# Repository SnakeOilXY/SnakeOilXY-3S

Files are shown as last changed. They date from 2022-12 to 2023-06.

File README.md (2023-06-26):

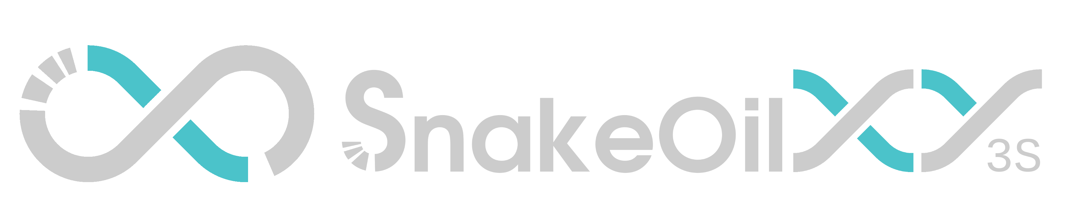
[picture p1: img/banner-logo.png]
Banner-logo


<a href="https://discord.gg/WZVP2HuAag" style="height: 40px !important;">Join us on Discord</a>

<a href='https://www.amazon.jp/hz/wishlist/ls/2AHXTCG01RYAZ?ref_=wl_share' target='_blank'>Buy Me a spool at amazon Japan</a>
<a href='https://www.printables.com/model/348118-snakeoilxy-3s/files' target='_blank'>download link</a>

# SnakeOilXY-3S
Entry level, low cost mod for Kingroon KP3S 3D printer.

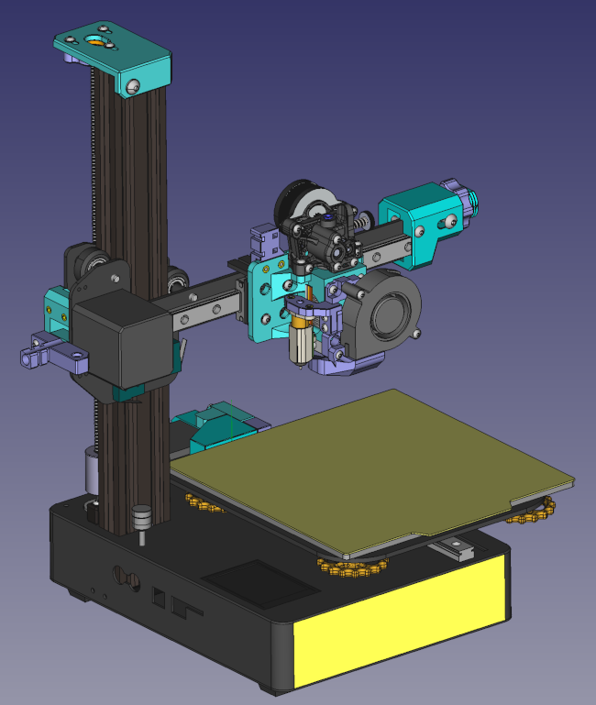
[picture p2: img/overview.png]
overview


## 1. Introduction

Kingroon KP3S is a nice small printer, but it comes with some mechanical design problems. This mod is aiming at fixing there problem with the lowest cost as possible.

__*This mod is for people already bought the KP3/S. DO NOT buy the KP3/S just because of this mod. There are many better printers you can build with the same price. For example [The Tic-Tac](https://www.printables.com/model/164038-tic-tac-miniaturised-v-minion)__

__*This mod is designed by measuring the real hardware of the first revision of the KP3(the model with Creality style direct red extruder). Some parts might need some minnor modify to fit other revisons of the machine.__

## 2. The problems and solutions

### 2.1. X and Y axis

- There is no proper way to adjust the belt tension of X and Y axis
- The belt path is not straight. This will affect the printed part dimension based on where it printed on the build place, special on large model.

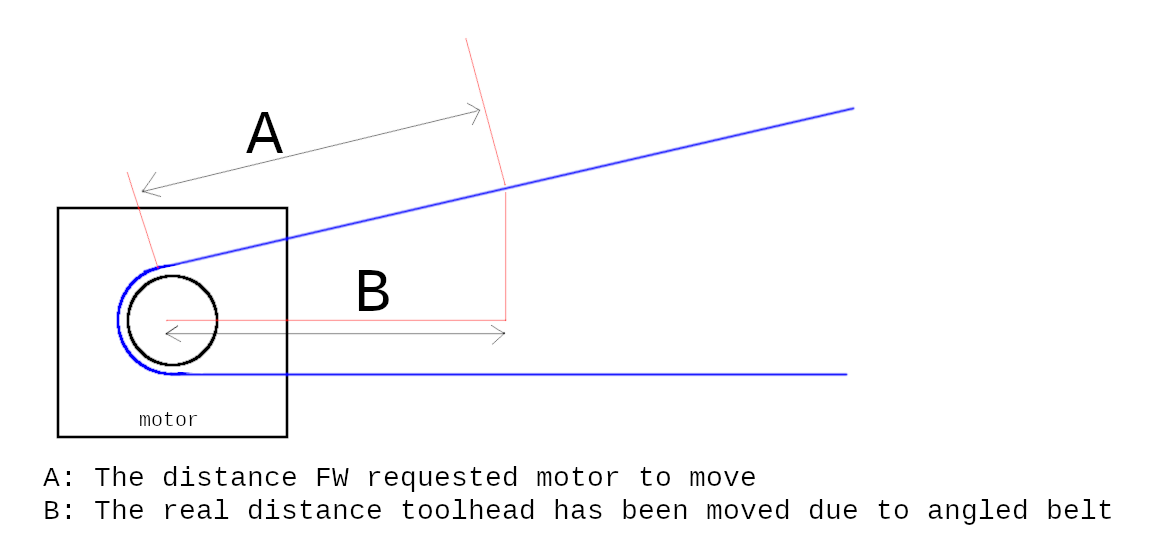
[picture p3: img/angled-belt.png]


- This mod added belt tensioner for X and Y axis.
- Change the belt mounting method to make the belt path straight.(check image bellow, this method apply for both X and Y belt).
- All motor shafts are supported by bearing.
- You will need new belts for XY tensioner mod since the belt path is a little longer than the original design. If not using my toolhead, you might need to your toolhead mounter to get full X movement.

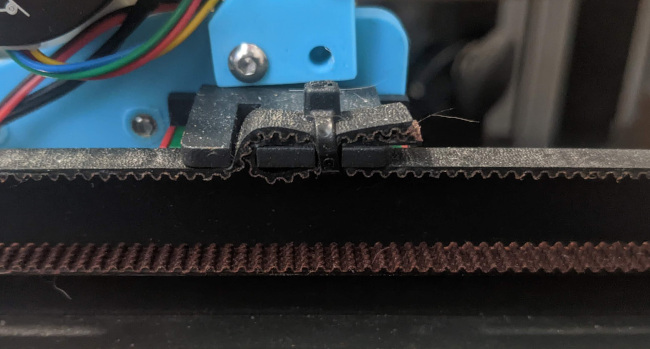
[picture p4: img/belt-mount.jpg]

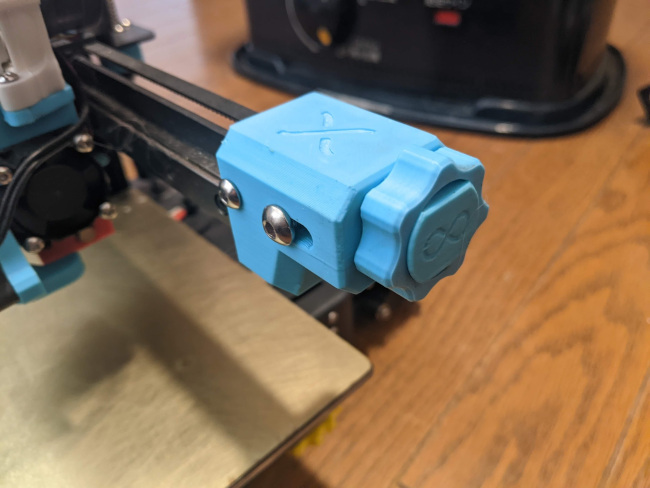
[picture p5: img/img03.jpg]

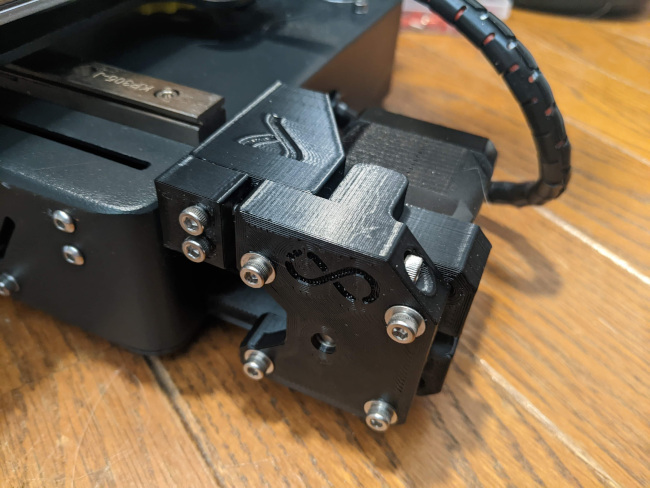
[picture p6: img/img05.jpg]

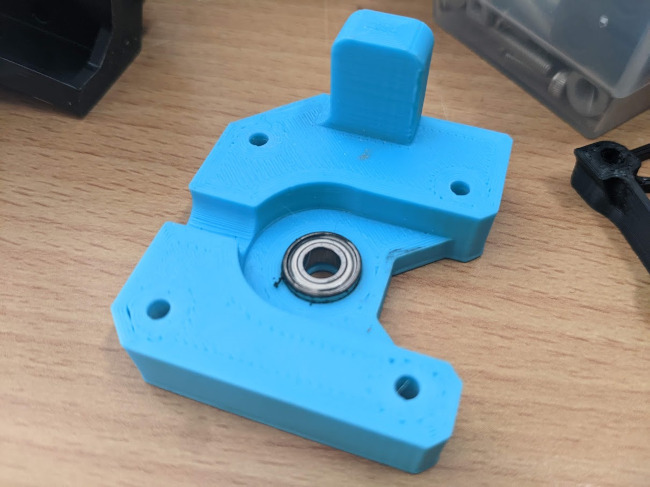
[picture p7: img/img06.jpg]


### 2.2. Z axis

- On some revisions of KP3/S the Z motor center and leadscrew nut are not well aligned. This will make the leadscew wobble and result in Z banding problem. 
- This mod added Oldham coupler and Position adjustable top support bearing. 
- Position adjustable top support bearing will allow to fine-adjust the leadscrew position so it parallel to the Z v-slot extrusion.
- Oldham coulper will deal with axial and angular misalignments of the leadscew nut.

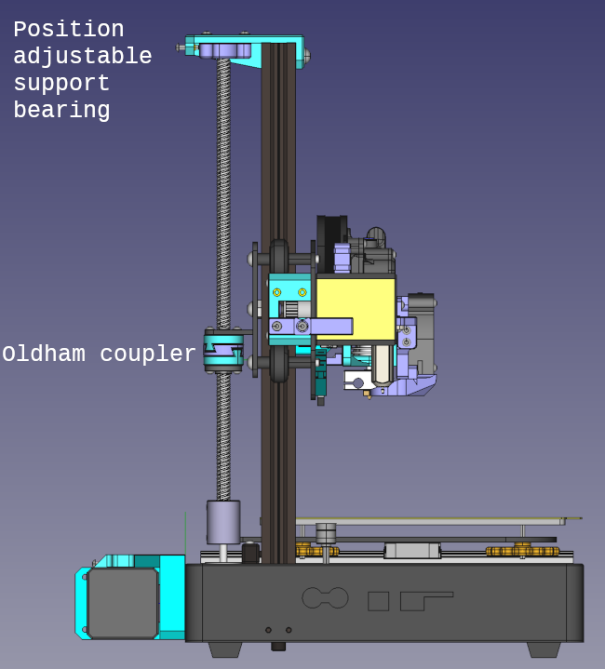
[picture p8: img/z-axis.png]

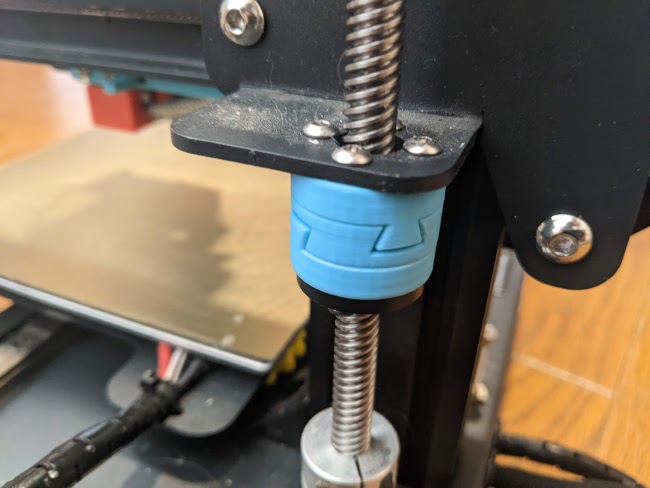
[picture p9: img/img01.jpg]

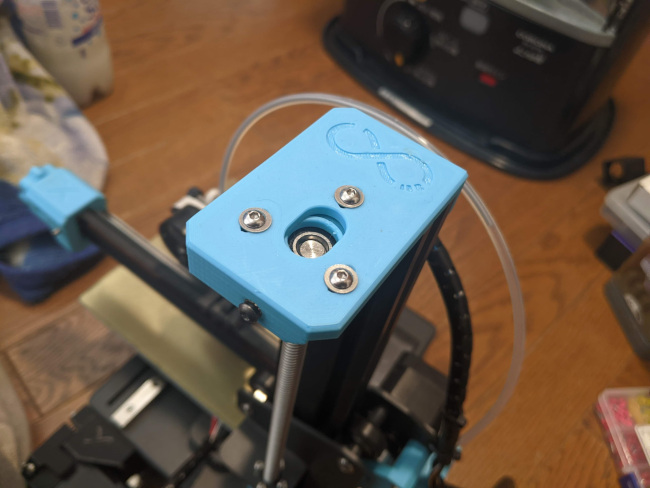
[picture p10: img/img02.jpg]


### 2.3. E axis (optional)

- There is no problem with the original extruder except it too heavy for the unsupported gantry. 
- This mod added 2 options for lighter extruder: Direct drive Sherpa mini mount and bowden extruder mount. 
- The above extruder mounters can be use with V6 hotend or any other hotend using the same mounting method(Dragon hotend with groove adapter for example).
- Optional mounting slot for BLtouch/3Dtouch
- Compatible with [bear_extruder_and_x_axis](https://github.com/gregsaun/bear_extruder_and_x_axis) fan duct and other 3rd party ducts like [RH_Dreambox's Air nozzle for the Bear extruder (Rev.1)](https://www.thingiverse.com/thing:3390107) or [MajorOCD's Fan Duct for Bear Extruder](https://www.thingiverse.com/thing:3855570)

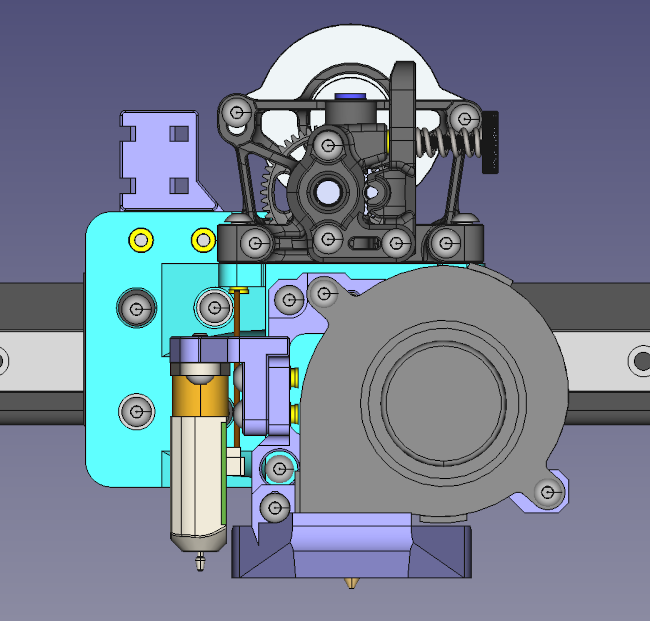
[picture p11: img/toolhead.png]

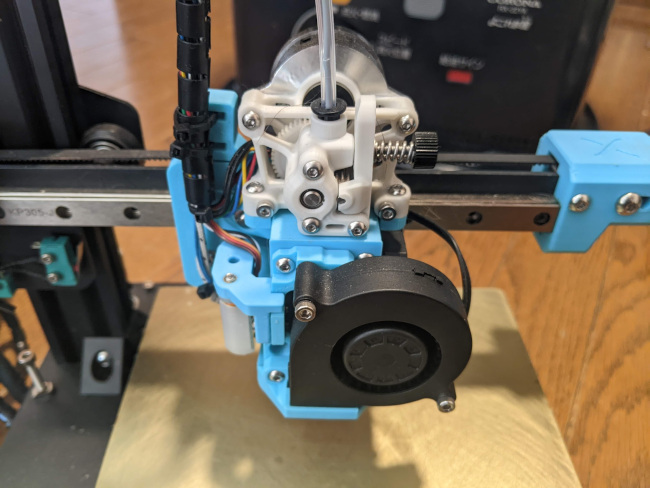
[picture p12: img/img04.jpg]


### 2.4. Klipper config

- will be added soon

## 3. Bill of materials

<table>
    <thead>
        <tr>
            <th>Item</th>
            <th>Quantity</th>
            <th>Description</th>
            <th>link</th>
        </tr>
    </thead>
    <tbody>
        <tr>
            <td>M3x4-HeatSet</td>
            <td>100</td>
            <td>M3 X D4.2 X L4.0</td>
            <td><a href="https://s.click.aliexpress.com/e/_Ad1n92" rel="nofollow">Aliexpress</a></td>
        </tr>
        <tr>
            <td>MR115 bearing</td>
            <td>2</td>
            <td></td>
            <td><a href="https://s.click.aliexpress.com/e/_De3O1rt" rel="nofollow">Aliexpress</a></td>
        </tr>
        <tr>
            <td>688 bearing</td>
            <td>1</td>
            <td></td>
            <td><a href="https://s.click.aliexpress.com/e/_Dd0g23b" rel="nofollow">Aliexpress</a></td>
        </tr>
        <tr>
            <td>20T 6mm Tooth Idler (5mm bore)</td>
            <td>2</td>
            <td>Only E3D's Gates idler or Mellow's Gates idler will fit</td>
            <td><a href="https://www.aliexpress.com/item/33023133633.html" rel="nofollow">Aliexpress</a></td>
        </tr>
        <tr>
            <td>6mm 2GT belt</td>
            <td>1.5~2m</td>
            <td>M3 X D4.2 X L4.0</td>
            <td><a href="https://www.Aliexpress.com/item/32952396111.html" rel="nofollow">Aliexpress</a></td>
        </tr>
        <tr>
            <td>4x5x12mm brass tube (IDxODxLength)</td>
            <td>1</td>
            <td>Can be cuted from longer tube</td>
            <td><a href="https://s.click.aliexpress.com/e/_DC6Dbc3" rel="nofollow">Aliexpress</a></td>
        </tr>
        <tr>
            <td>2.5mm wide ziptie</td>
            <td>1 pack</td>
            <td></td>
            <td></td>
        </tr>
        <tr>
            <td>Sherpa mini extruder kit</td>
            <td>1</td>
            <td>Direct extruder parts - OPTIONAL</td>
            <td><a href="https://s.click.aliexpress.com/e/_DmmcVKn" rel="nofollow">Aliexpress</a></td>
        </tr>
        <tr>
            <td>5015 blower fan</td>
            <td>1</td>
            <td>Direct extruder parts - OPTIONAL</td>
            <td><a href="https://s.click.aliexpress.com/e/_DllkWdp" rel="nofollow">Aliexpress</a></td>
        </tr>
        <tr>
            <td>3010 fan</td>
            <td>1</td>
            <td>Direct extruder parts - OPTIONAL</td>
            <td><a href="https://s.click.aliexpress.com/e/_DlSF5np" rel="nofollow">Aliexpress</a></td>
        </tr>
        <tr>
            <td>PTFE tube clip set</td>
            <td>2</td>
            <td>Extruder parts - OPTIONAL</td>
            <td><a href="https://s.click.aliexpress.com/e/_DEVMtuF" rel="nofollow">Aliexpress</a></td>
        </tr>
        <tr>
            <td>Bolts and nuts</td>
            <td>?</td>
            <td>Work-in-Progress</td>
            <td></td>
        </tr>
    </tbody>
</table>

## 4. How to print parts

- PETG, ABS or PC filament depend on your budget and how hot you will run the printer.
- 0,4mm nozzle, 0.2mm layer height, 5 walls, 30% infill
- Oldham coupler will need to be printed with small layer height(0.05~0.1mm) and small diameter nozzle(~0.25mm) if possible. This parts will need some sanding to make the mating surface smooth enough.

## 5. Copyright Notice

- [Sherpa mini extruder](https://github.com/Annex-Engineering/Sherpa_Mini-Extruder) is an original work of [Annex Engineering](https://github.com/Annex-Engineering), modified parts using their source code/design files are re-released under [ANNEX Engineering License](https://github.com/Annex-Engineering/ANNEX-Engineering-License-Agreement/blob/main/LICENSE.md).
- [bear_extruder_and_x_axis](https://github.com/gregsaun/bear_extruder_and_x_axis) is an original work of [Grégoire Saunier](https://github.com/gregsaun), modified parts using their source code/design files are re-released under [GNU General Public License v3.0](https://github.com/gregsaun/bear_extruder_and_x_axis/blob/master/LICENSE)
- The CAD assembly using Kingroon KP3/S model of [Fukuma Yohei](https://www.thingiverse.com/fukumay/designs) at [Thingiverse - Kingroon KP3S full assembly STP/OBJ data](https://www.thingiverse.com/thing:4889303) under [Creative Commons - Attribution license](https://creativecommons.org/licenses/by/4.0/)
- This printer design(SnakeOilXY-3S), it's document and software are released under [GNU General Public License v3.0](https://github.com/ChipCE/SnakeOil-XY/blob/master/LICENSE)

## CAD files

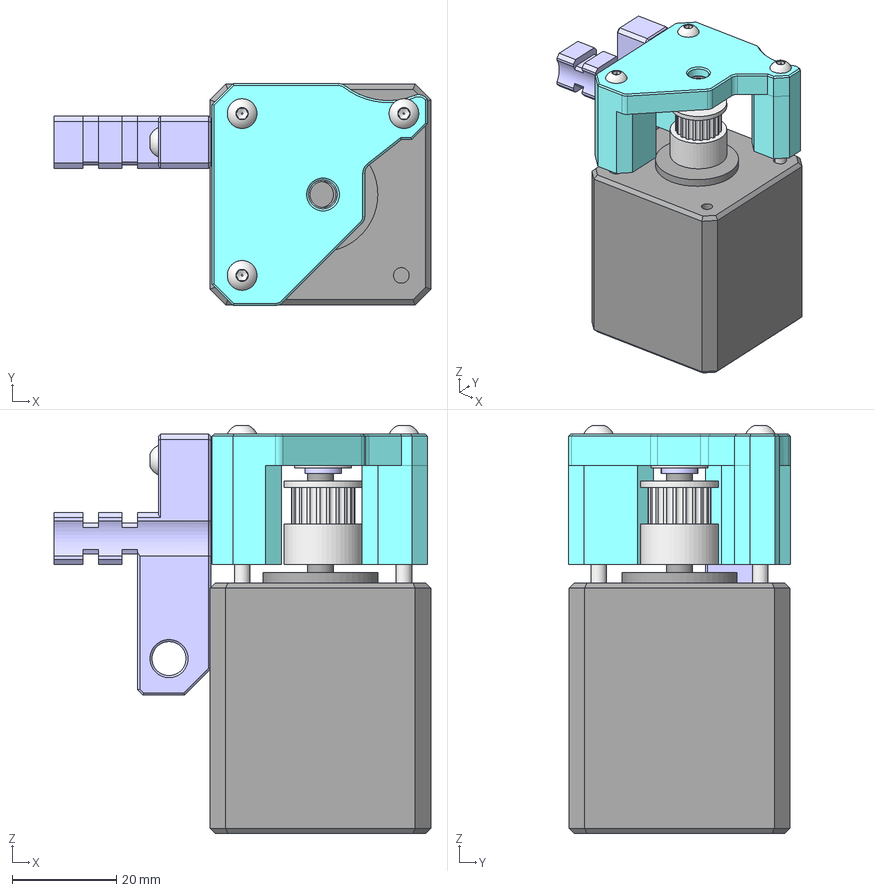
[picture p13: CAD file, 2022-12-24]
src/component-assembly/x-motor-support-assembly.FCStd
72.2 x 42.5 x 78.2 mm
x-motor-support
direct-drive-extruder-cable-mount
M3x30-Screw
M3x30-Screw003
M3x30-Screw004
M3x30-Screw005
M3-Insert
M3-Insert004
M3-Insert005
M3-Insert006
M3x12-Screw
MR115ZZ-bearing
stepper-motor
6mm-pulley
spacer-1mm

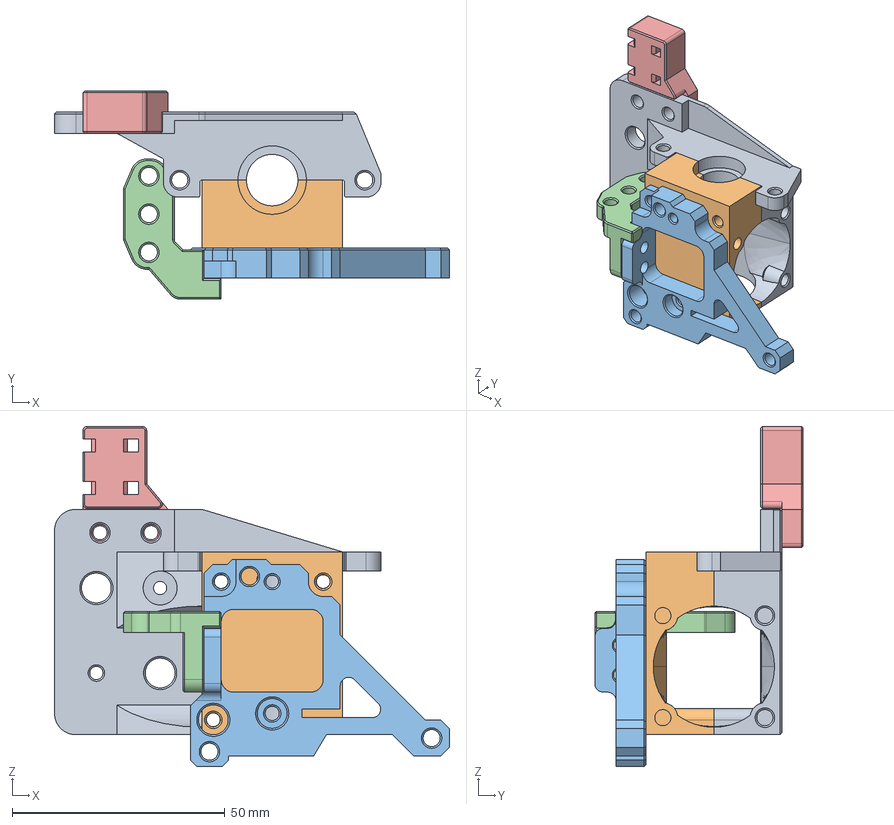
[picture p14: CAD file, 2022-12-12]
WIP/component-assembly/toolhead-assembly.FCStd
92.9 x 49.0 x 80.0 mm
back-body-direct
front-body
fan-mounter001
cable-mounter001

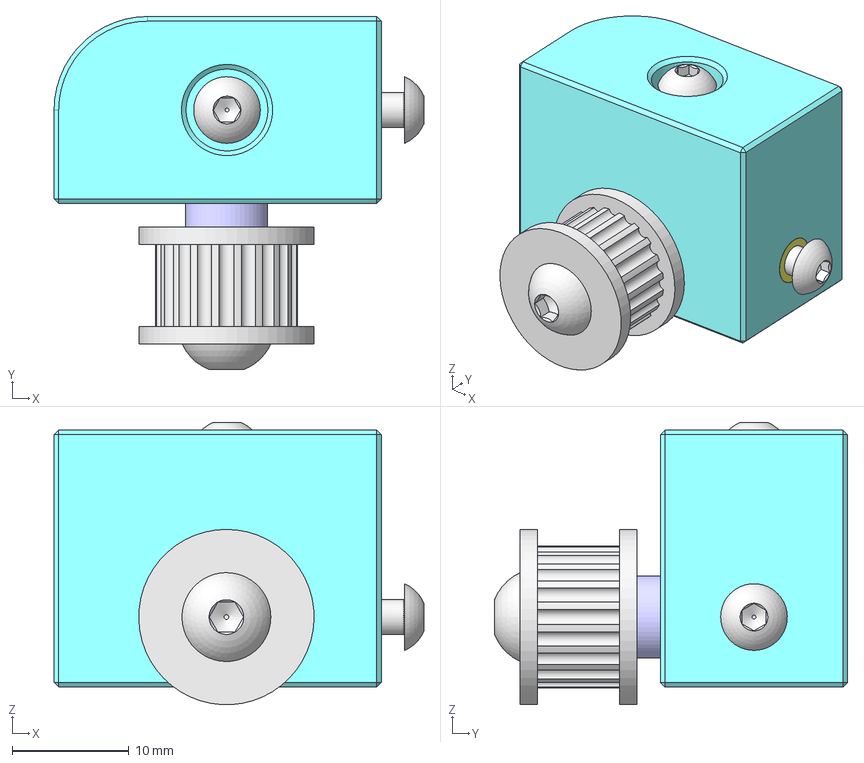
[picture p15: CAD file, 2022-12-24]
src/component-assembly/y-idler-supporter-assembly.FCStd
31.7 x 30.2 x 24.1 mm
shaft-supporter
spacer-2mm
6mm-tooth-idler001
brass-tube-4x5x12
M4x20-Screw
M3-HeatSet
M3-HeatSet001
M3x10-Screw
M3x12-Screw

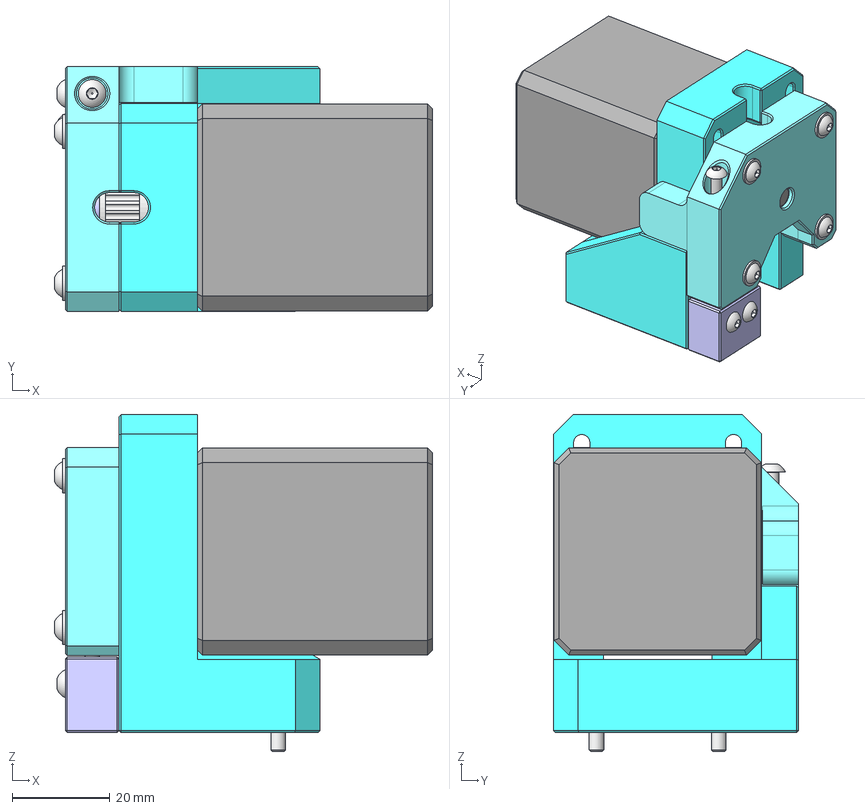
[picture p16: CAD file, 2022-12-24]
src/component-assembly/y-motor-mount-assembly.FCStd
77.2 x 50.0 x 68.8 mm
y-motor-mounter
y-motor-cap
tesioner-block
MR115ZZ-bearing
stepper-motor
M3-Insert
M3-Insert001
M3-Insert002
M3-Washer
M3-Washer001
M3-Washer002
M3-Washer003
M3x30-Screw
M3x30-Screw004
M3x30-Screw005
M3x30-Screw006
M3x30-Screw009
M3x30-Screw010
M3x40-Screw
M3-Washer006
M3-Washer007
M3x16-Screw
M3x16-Screw001
6mm-pulley
spacer-1mm

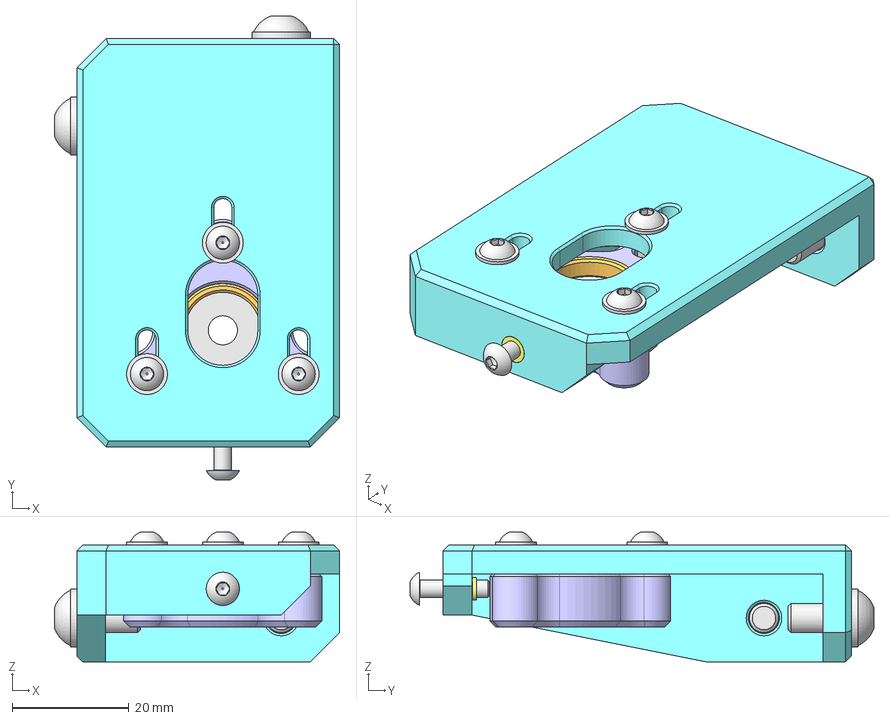
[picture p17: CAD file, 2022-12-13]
src/component-assembly/z-top-bearing-assembly.FCStd
48.9 x 79.5 x 22.2 mm
spacer
bearing-housing
M3-Insert
M3-Insert001
M3-Insert002
M3-Insert003
M3x12-Screw
M3-Washer
M3-Washer005
M3-Washer006
M3x14-Screw
M3x14-Screw003
M3x14-Screw004
M5-Washer
M5-Washer001
M5x12-Screw
M5x12-Screw001
top-plate
625-bearing

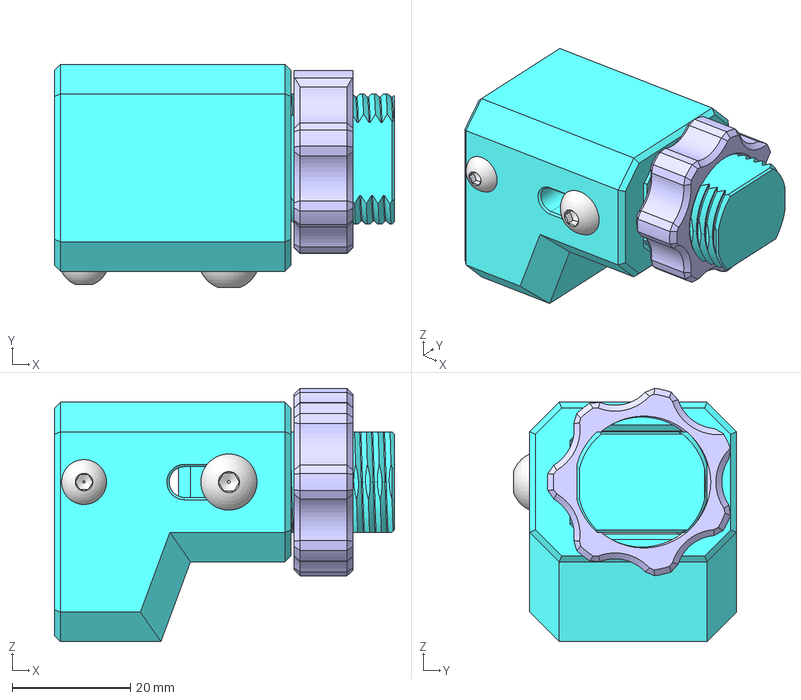
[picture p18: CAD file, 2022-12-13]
src/component-assembly/x-tesioner-assembly.FCStd
57.5 x 37.8 x 42.9 mm
pulley-housing
tensioner-body
tesioner-nut
M4x35-Screw
M5x35-Screw
6mm-tooth-idler001

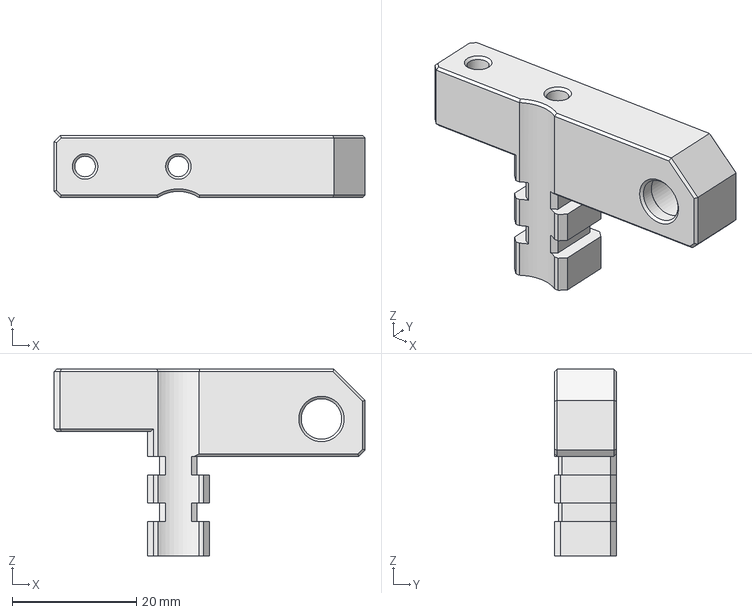
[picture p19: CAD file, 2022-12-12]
src/E-axis/direct-extruder-cable-mounter.FCStd
50.0 x 10.0 x 30.0 mm

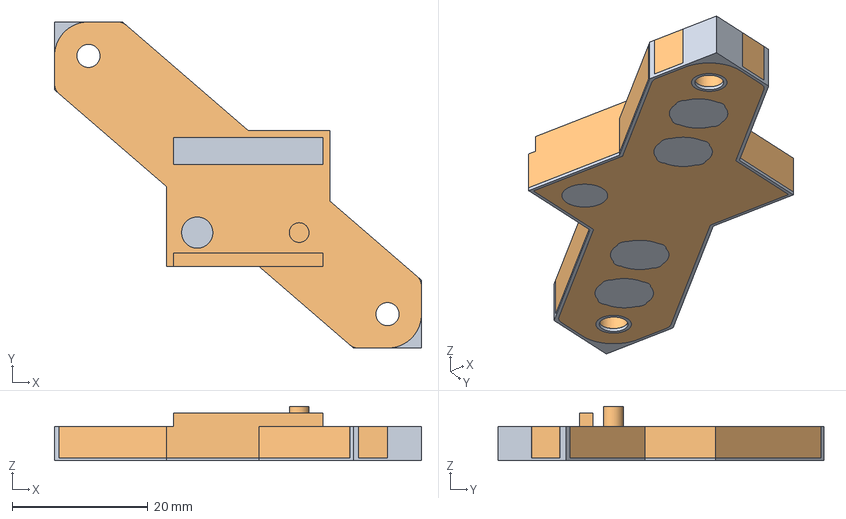
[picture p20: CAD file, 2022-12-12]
src/Other/adxl345-mounter.FCStd
54.0 x 48.0 x 8.00 mm

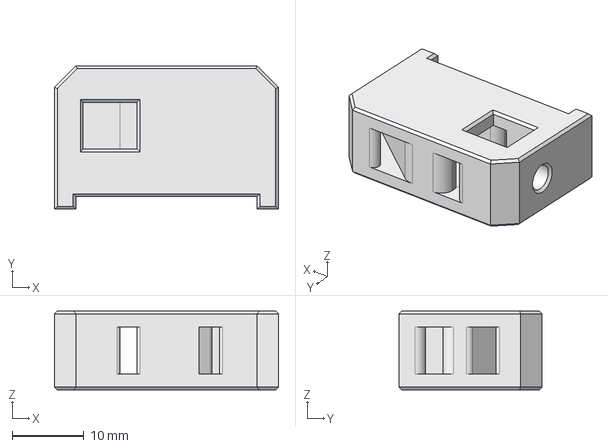
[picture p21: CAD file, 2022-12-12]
src/X-axis/belt-clip-tesioner.FCStd
31.3 x 20.0 x 11.0 mm

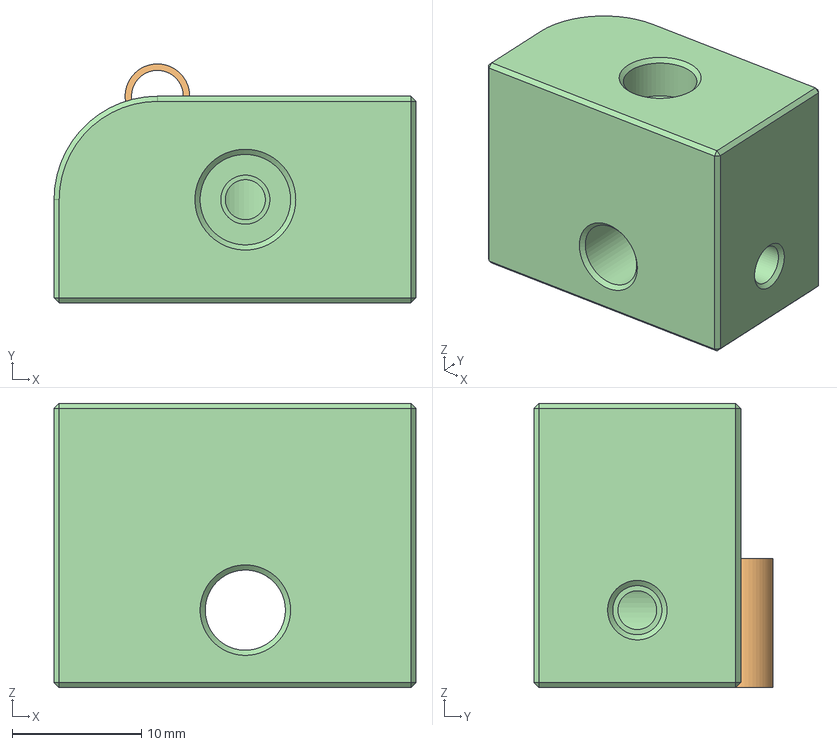
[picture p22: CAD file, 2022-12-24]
src/Y-axis/idler-supporter.FCStd
28.0 x 18.5 x 22.0 mm
brass-tube
brass-tube001

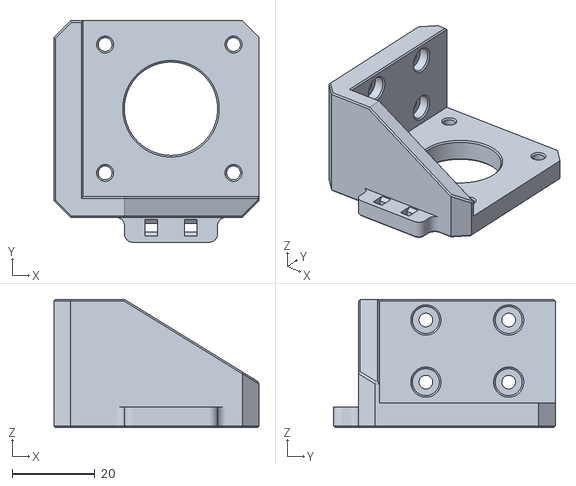
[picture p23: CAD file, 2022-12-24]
STLs/E-axis/OPTIONAL_1x_bowden-e-motor-mount.stl
49.5 x 53.5 x 31.0

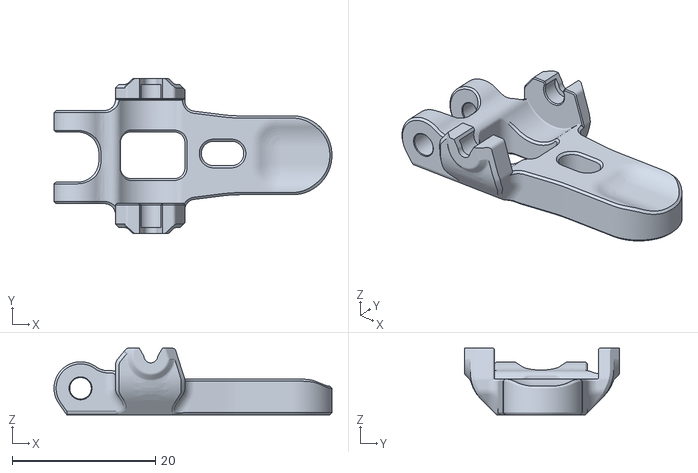
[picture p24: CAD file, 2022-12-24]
STLs/E-axis/sherpa-mini-extruder/filament-arm.stl
38.8 x 21.6 x 9.30

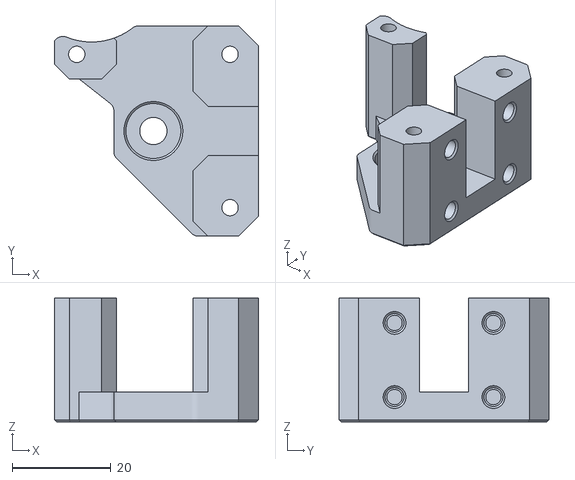
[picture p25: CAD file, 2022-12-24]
STLs/X-axis/x1_x-motor-support.stl
41.2 x 42.5 x 25.0

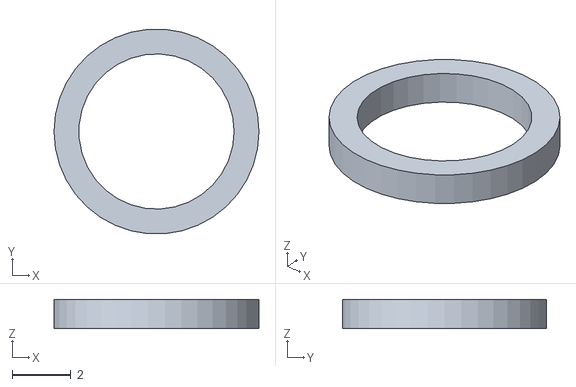
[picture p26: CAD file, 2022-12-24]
STLs/Y-axis/x1_motor-shaft-spacer.stl
7.00 x 6.98 x 1.00

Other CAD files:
STLs/Z-axis/x1_z-bearing-housing.stl
src/E-axis/back-body-bowden.FCStd
src/Other/belt-extra-mounter.FCStd
src/X-axis/x-belt-tensioner.FCStd
STLs/E-axis/1x_back-body-for-direct-drive.stl
STLs/E-axis/1x_bear-duct.stl
STLs/E-axis/1x_bltouch-mount.stl
STLs/E-axis/1x_cable-mounter.stl
STLs/E-axis/1x_front-body.stl
STLs/E-axis/1x_mounting-plate.stl
STLs/E-axis/1x_x-endstop.stl
STLs/E-axis/OPTIONAL_1x_back-body-for-bowden.stl
STLs/E-axis/sherpa-mini-extruder/back-body.stl
STLs/E-axis/sherpa-mini-extruder/front-body.stl
STLs/E-axis/x1_direct-drive-extruder-cable-mount.stl
STLs/X-axis/1x_idler-housing.stl
STLs/X-axis/1x_tesioner-body.stl
STLs/X-axis/x1_tesioner-nut.stl
STLs/Y-axis/1x_y-motor-cap.stl
STLs/Y-axis/1x_y-motor-mounter.stl
STLs/Y-axis/x1_idler-shaft-spacer.stl
STLs/Y-axis/x1_shaft-supporter.stl
STLs/Y-axis/x1_tesioner-block.stl
STLs/Z-axis/1x_z-top-plate.stl
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

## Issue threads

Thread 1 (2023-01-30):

Problem with inner y-belt mount

pr0phe, 2023-01-30:
Hi there. I've heard there is a problem with inner y-belt mount, that flex due to y-tensioner.
Do you have any improvements for that case?

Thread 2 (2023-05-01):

Not compatible with Kingroon KP3

PSLLSP, 2023-05-01:
This mod declares it is for Kingroon KP3 but it is not compatible with KP3 at all.
Kingroon KP3 is 3D printer that has display at angle 45 degree and linear rail is only at Y axis. Y belt is not hidden in the base box. X-end switch is mounted on X-motor cover. It has bowden extruder and hot end is similar to Ender design.

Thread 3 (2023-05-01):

Filename rules

PSLLSP, 2023-05-01:
Please, standardize rules for filenames of STL files, I see two different patterns, like

`1x_tesioner-body.stl` and `x1_motor-shaft-spacer.stl`

I assume that `1x` and `x1` means that that part should be printed only once. Please, define policy `1x`, `2x` or `x1`, `x2` and rename all files to comply with that policy... I think that `1x` is better than `x1`. Then filenames should look like this:
`1x_tesioner-body.stl` and `1x_motor-shaft-spacer.stl` (or even fix a typo, then `1x_tensioner-body.stl` ;-)

Or prefer '`x1`, than filenames should look like this: `x1_tesioner-body.stl` and `x1_motor-shaft-spacer.stl`

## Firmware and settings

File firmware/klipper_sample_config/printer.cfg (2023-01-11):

# Gcode and custom macros
[include gcode.cfg]
[include macro.cfg]
# Custom LCD menu
[include menu.cfg]
[include display.cfg]
# Shell command 
[include shell_command.cfg]

# [mcu rpi]
# serial: /tmp/klipper_host_mcu

# [adxl345]
# cs_pin: rpi:None

# [resonance_tester]
# accel_chip: adxl345
# probe_points:
#     90,90,20

[mcu]
serial: /dev/serial/by-id/usb-1a86_USB_Serial-if00-port0
baud: 250000
restart_method: command

[printer]
kinematics: cartesian
max_velocity: 300
max_accel: 15000
max_accel_to_decel:5000
max_z_velocity: 15
max_z_accel: 100
square_corner_velocity: 5.0



[stepper_x]
step_pin: PE3
dir_pin: PE2
enable_pin: !PE4
full_steps_per_rotation: 200
microsteps: 32
rotation_distance: 40
endstop_pin: !PA15
position_endstop: 0
position_min: 0
position_max: 180
homing_speed: 50
homing_retract_dist: 0
second_homing_speed: 3

[tmc2208 stepper_x]
uart_pin: PA3
run_current: 0.650
hold_current: 0.6
stealthchop_threshold: 0
# interpolate: false
# sense_resistor: 0.110


[stepper_y]
step_pin: PE0
dir_pin: PB9
enable_pin: !PE1
full_steps_per_rotation: 200
microsteps: 32
rotation_distance: 40
endstop_pin: !PA12
position_endstop: -2.5
position_min: -2.5
position_max: 180
homing_speed: 50
homing_retract_dist: 0
second_homing_speed: 3

[tmc2208 stepper_y]
uart_pin: PA6
run_current: 0.650
hold_current: 0.6
stealthchop_threshold: 0
# interpolate: false
# sense_resistor: 0.110

[stepper_z]
step_pin: PB5
dir_pin: !PB4
enable_pin: !PB8
full_steps_per_rotation: 200
microsteps: 32
rotation_distance: 8
endstop_pin: !PA11 # disable to use BLTouch
# endstop_pin: probe:z_virtual_endstop  # enable to use BLTouch
position_endstop: 0 # disable to use BLTouch
position_max: 190
homing_retract_dist: 10.0
second_homing_speed: 5
# position_min: -5 # enable to use BLTouch

# [tmc2208 stepper_z]
# uart_pin: PB13
# run_current: 0.650
# hold_current: 0.6
# stealthchop_threshold: 9999
# interpolate: false
# sense_resistor: 0.110


[extruder]
step_pin: PD6
dir_pin: !PD3
enable_pin: !PB3
full_steps_per_rotation: 200
microsteps: 32
rotation_distance: 31.776 #red head
nozzle_diameter: 0.400
filament_diameter: 1.750
heater_pin: PC3
sensor_type: ATC Semitec 104NT-4-R025H42G
sensor_pin: PC1
control: pid
pid_Kp: 19.0
pid_Ki: 1.34
pid_Kd: 67.5
min_temp: 0
max_temp: 300
pressure_advance: 0.05

[tmc2208 extruder]
uart_pin: PA1
run_current: 0.500
hold_current: 0.250
# sense_resistor: 0.110
stealthchop_threshold: 0
# interpolate: false
# sense_resistor: 0.110


#[probe]
#pin: PC5
#deactivate_on_each_sample: True
#x_offset: -28
#y_offset: -21
#z_offset: 0.0
#speed: 20
#samples: 4
#sample_retract_dist: 1
#samples_result: median
#   The calculation method when sampling more than once - either
#   "median" or "average". The default is average.
#samples_tolerance: 0.050
#samples_tolerance_retries: 2
#activate_gcode:
#deactivate_gcode:

#[bltouch]
#sensor_pin: ^PB7
#control_pin: PB6
#stow_on_each_sample: False
#probe_with_touch_mode: True
#x_offset: -28
#y_offset: -21
#z_offset: 1.800
#speed: 10 ;8
#sample_retract_dist: 3
#samples_result: median
#samples: 3

[heater_bed]
heater_pin: PA0
sensor_type: Kingroon_Calibrated B3950
sensor_pin: PC0
control: pid
pid_Kp: 40.68
pid_Ki: 7.93
pid_Kd: 139.15
min_temp: 0
max_temp: 130

##	Hotend Fan --> FAN5
[heater_fan hotend_fan]
pin: PB0
heater: extruder
heater_temp: 50.0
fan_speed: 1.0
shutdown_speed: 1

##	Part Cooling Fan --> FAN4
[fan]
pin: PB1
kick_start_time: 0.5
#off_below: 0.25


##	mini12864 LCD Display
#[display]
#lcd_type: uc1701
#cs_pin: PE9
#a0_pin: PE10
#rst_pin: PE12
#encoder_pins: ^PB1, ^PB2
#click_pin: ^!PE7
#contrast: 63
#spi_software_miso_pin: PA6
#spi_software_mosi_pin: PA7
#spi_software_sclk_pin: PA5
#menu_timeout: 300
#menu_reverse_navigation: False
#menu_root: __menutree
#display_group: _custom_12864_16x4

#[neopixel lcd_led]
#pin: PE13
#chain_count: 3
#initial_RED: 1.0
#initial_GREEN: 1.0
#initial_BLUE: 0.5
#initial_WHITE: 1.0
#color_order: RGB

#[output_pin BEEPER_pin]
#pin: PE8
#pwm: True
#value: 0
#shutdown_value: 0
#cycle_time: 0.001
#scale: 1000

#[neopixel led]
#pin: PB0
#chain_count: 20
#initial_RED: 0.6
#initial_GREEN: 1.0
#initial_BLUE: 1.0
#initial_WHITE: 1.0

[bed_screws]
#need calibration
screw1: 20,20
screw2: 160,20
screw3: 160,160
screw4: 20,160


[safe_z_home]
home_xy_position: 85,85 # Change coordinates to the center of your print bed
speed: 100
z_hop: 15                 # Move up 15mm
z_hop_speed: 15


[bed_mesh]
speed: 100
horizontal_move_z: 3 ; 10 for bltouch
mesh_min: 0,0 # prob pos
mesh_max: 150, 180 # prob pos
probe_count: 6 ; 
algorithm: bicubic

[virtual_sdcard]
path: ~/gcode_files


[pause_resume]
recover_velocity: 50


[display_status]

#[idle_timeout]
#timeout: 1800
#gcode:
#  UPDATE_DELAYED_GCODE ID=POWER_DOWN DURATION=1 ; call auto power down after print done or canceled

[respond]
# enable M118 and RESPONSE command

[force_move]
enable_force_move: True

#[input_shaper]
#shaper_freq_x: 78.6
#shaper_type_x: mzv
#shaper_freq_y: 52.6
#shaper_type_y: mzv

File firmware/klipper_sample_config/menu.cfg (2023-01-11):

# This file defines the default layout of the printer's menu.

# It is not necessary to edit this file to change the menu. Instead,
# one may override any of the sections defined here by defining a
# section with the same name in the main printer.cfg config file.

### DEFAULT MENU ###
# Main
#   + Tune
#       + Z offset
#          + Offset Z:00.00
#          + Save offset
#       + Adt.Speed : ON/OFF
#       + Speed: 000%
#       + Flow: 000%
#   + SD Card
#       + Start
#       + Resume
#       + Pause
#       + Abort
#       + ... (files)
#   + Motion
#       + Home
#           + Home All
#           + Home X/Y
#           + Home Z
#       + Move
#          + Move X:000.0
#          + Move Y:000.0
#          + Move Z:000.0
#          + Move E:+000.0
#          + Bed Up   10mm
#          + Bed Down 10mm
#       + Align Z
#       + Steppers off
#       + Align Z
#       + Disable steppers
#   + Cooling
#       + Layer fan
#       + Bed fan
#       + Filter fan
#   + Temperature
#       + Cooldown
#           + Cooldown all
#           + Cooldown hotend
#           + Cooldown hotbed
#       + Ex0:000 (0000)
#       + Ex1:000 (0000)
#       + Bed:000 (0000)
#       + Preheat PLA
#           + Preheat all
#           + Preheat hotend
#           + Preheat hotbed
#       + Preheat PETG
#           + Preheat all
#           + Preheat hotend
#           + Preheat hotbed
#       + Preheat ABS
#           + Preheat all
#           + Preheat hotend
#           + Preheat hotbed
#   + Filament
#       + Ex0:000 (0000)
#       + Load Fil.
#       + Unload Fil.
#       + Feed: 000.0
#       + Cooldown
#   + Setup
#       + Align Z
#       + Bed mesh
#       + Probe calibrate
#           + Start calibrate
#           + Adjust Z
#               + +1.0
#               + +0.1
#               + +0.05
#               + -1.0
#               + -0.1
#               + -0.05
#           + Accept
#           + Abort
#           + Save
#       + Probe acc. test
#       + PID tunning
#           + Tune Hotend PID
#           + Tune Hotbed PID
#       + Save(restart)
#       + Save(pending)
#       + Dump parameters
#       + Restart
#           + Restart host
#           + Restart FW
#   + System
#       + Reboot
#       + Shutdown

### menu main ###
[menu __menutree]
type: list
name: Main

### menu tune ###
[menu __menutree __tune]
type: list
enable: {printer.idle_timeout.state == "Printing"}
name: Tune

[menu __menutree __tune __zoffset]
type: list
enable: {printer.idle_timeout.state == "Printing"}
name: Z offset

[menu __menutree __tune __zoffset __adjust]
type: input
name: Offset Z:{'%05.3f' % menu.input}
input: {printer.gcode_move.homing_origin.z}
input_min: -5
input_max: 5
input_step: 0.005
realtime: True
gcode:
    SET_GCODE_OFFSET Z={'%.3f' % menu.input} MOVE=1

[menu __menutree __tune __zoffset __savelater]
type: command
name: Save offset
gcode:
    PLAY_SINGLE_FEEDBACK_SOUND
    ENABLE_SAVE_CONFIG

[menu __menutree __tune __toggle_adaptive_speed]
type: command
name: Adt.Speed: {% if printer["gcode_macro SHARE_VARIABLES"].enable_adaptive_speed %}ON{% else %}OFF{% endif %}
gcode:
    TOGGLE_ADAPTIVE_SPEED

[menu __menutree __tune __speed]
type: input
name: Speed: {'%3d' % (menu.input*100)}%
input: {printer.gcode_move.speed_factor}
input_min: 0
input_max: 5
input_step: 0.05
realtime: True
gcode:
    M220 S{'%d' % (menu.input*100)}

[menu __menutree __tune __flow]
type: input
name: Flow: {'%3d' % (menu.input*100)}%
input: {printer.gcode_move.extrude_factor}
input_min: 0
input_max: 2
input_step: 0.01
realtime: True
gcode:
    M221 S{'%d' % (menu.input*100)}

### menu virtual sdcard ###
[menu __menutree __sdcard]
type: vsdlist
enable: {('virtual_sdcard' in printer)}
name: SD Card

[menu __menutree __sdcard __start]
type: command
enable: {('virtual_sdcard' in printer) and (printer.print_stats.state == "standby" or printer.print_stats.state == "error" or printer.print_stats.state == "complete")}
name: Start
gcode:
    { menu.exit(True) }
    PLAY_SINGLE_FEEDBACK_SOUND
    M24

[menu __menutree __sdcard __resume]
type: command
enable: {('virtual_sdcard' in printer) and printer.print_stats.state == "paused"}
name: Resume
gcode:
    { menu.exit(True) }
    PLAY_SINGLE_FEEDBACK_SOUND
    RESUME

[menu __menutree __sdcard __pause]
type: command
enable: {('virtual_sdcard' in printer) and printer.print_stats.state == "printing"}
name: Pause
gcode:
    PLAY_SINGLE_FEEDBACK_SOUND
    { menu.exit(True) }
    PAUSE

[menu __menutree __sdcard __abort]
type: command
enable: {('virtual_sdcard' in printer) and (printer.print_stats.state == "printing" or printer.print_stats.state == "paused")}
name: Abort
gcode:
    { menu.exit(True) }
    CLEAR_PAUSE
    CANCEL_PRINT
    SDCARD_RESET_FILE

### menu control ###
[menu __menutree __motion]
type: list
name: Motion

[menu __menutree __motion __home]
type: list
name: Home
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

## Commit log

2022-12-24 added assembly and stl
    [1x_back-body-for-direct-drive.stl, 1x_bear-duct.stl, 1x_bltouch-mount.stl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]
2023-04-21 fix bom
2025-12-24 Update minimum quantities for bolts and nuts
    Added minimum quantity requirements for various bolts and nuts.
